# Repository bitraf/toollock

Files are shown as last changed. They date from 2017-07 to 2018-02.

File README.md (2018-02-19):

# TheLock
Electronic lock connected via wireless (Wi-Fi) and MQTT using [MsgFlo](https://msgflo.org).
The lock is intended to enforce 'checking out' and 'checking in' portable tools in a shared workshop environment.

It makes it possible to:

* Know whether a tool is currently in its station
* Checking for neccesary safety course before allowing usage
* Holding people responsible when equipment is not get returned or broken

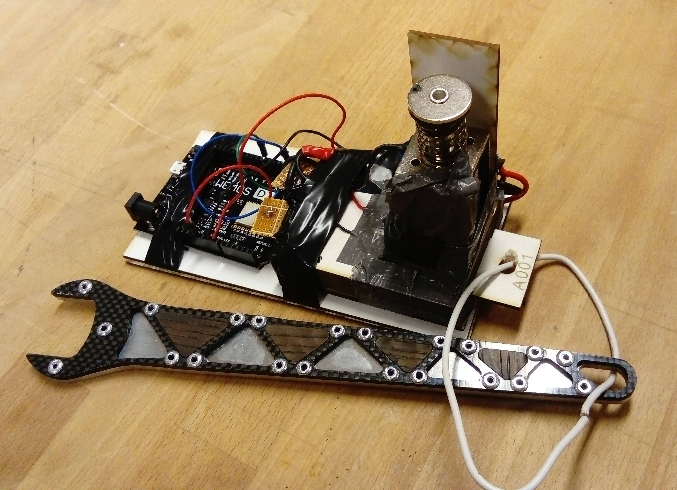
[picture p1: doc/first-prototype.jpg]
First funtional prototype


Each lock has a key with a matching key pattern. The key is physically attached to the tool using a wire.
An optical sensor detects that the right key is used. IR leds normally light through, only a matching key will fully block light.

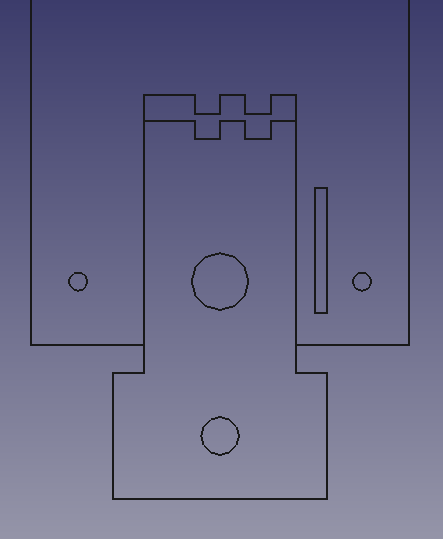
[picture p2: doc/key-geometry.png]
Key & lock geometry


The key and lock can be CNC-milled, lasercut or 3d-printed.

## Status
**Proof of concept**

* July 2017: Functional prototype was built during 2-day hackathon
* First production version planned for October 2017

## Bill of Materials

[Google Doc](https://docs.google.com/spreadsheets/d/1zNnj4h8AQoaYpxoNCeb7HHqZF6n6yWtV7tDY7eSM0z4/edit?usp=sharing)

* Microcontroller - ESP8266 or similar. We used a Wemos D1 board.
* actuator - we used a solenoid that is rated for 12V (it actually actuates at about 7V, but slowly), it draws about 0.3 - 0.7 A. Alternatives:
[1](https://www.banggood.com/12V-24V-Electronic-Door-Lock-Rfid-Access-Control-for-Cabinet-Drawer-p-1011146.html)
[2](https://www.banggood.com/12V-DC-Cabinet-Door-Drawer-Electric-Lock-Assembly-Solenoid-Lock-27x29x18mm-p-1048590.html)
* mosfet - we used a IPP055N03L
* resistor - a 10k ohm resistor for pulldown on the control signal
* power supply - a 12V DC power supply for the actuator / solenoid
* IR led 0805, 120deg. [Kingbright kp-2012f3c](http://no.farnell.com/kingbright/kp-2012f3c/led-ir-0805-940nm/dp/2290432)
* IR phototransistor 0805, 120 deg. [Kingbright kp-2012p3c](http://no.farnell.com/kingbright/kp-2012p3c/phototransistor-0805-940nm/dp/2290434)

https://wiki.wemos.cc/products:d1:d1_mini
https://github.com/esp8266/esp8266-wiki/wiki/Pin-definition

## Setup firmware

* Install Arduino libraries [PubsubClient](https://github.com/knolleary/pubsubclient) and [Msgflo](https://github.com/msgflo/msgflo-arduino)
* Setup wifi connection: Add a file `Config.h` defining parameters `WIFI_SSID` and `WIFI_PASSWORD`
* Configure MQTT details in the sketch

## TODO

v1.0: First fabricated version

* Electronics: Switch to a standard transmissive detector, PCB mounted.
* Mechanics: Update to vertical PCB orientation, check connections
* Produce initial 4 locks
* Mechanics: Add a casing/box for 4-8 locks. Securely wall/table mountable.

## License
MIT

## Made by

[einsmein](https://github.com/einsmein), [tingox](https://github.com/tingox) and [jonnor](https://github.com/jonnor)

## State machine

State machine diagram

## Electronics

Developed in KiCAD.
Schemantic used for first protototype

## Mechanics

Developed in FreeCAD.
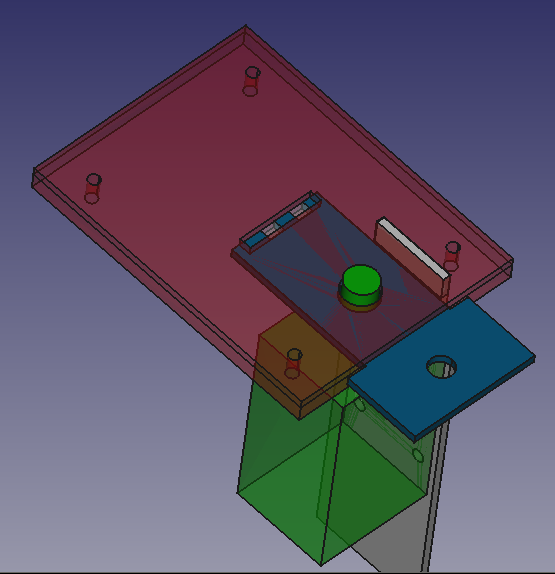
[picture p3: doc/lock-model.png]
Lock model


SIG: gnd+in
PWR: 12v+gnd
OUT: 12v+out

IN
GND
12v
12v
OUT

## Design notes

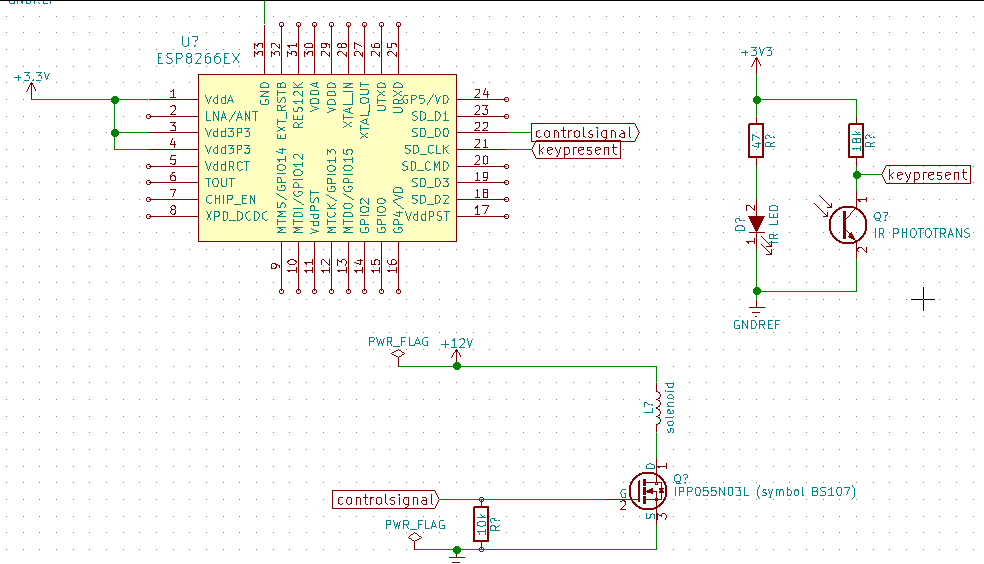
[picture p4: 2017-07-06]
doc/schematic.png

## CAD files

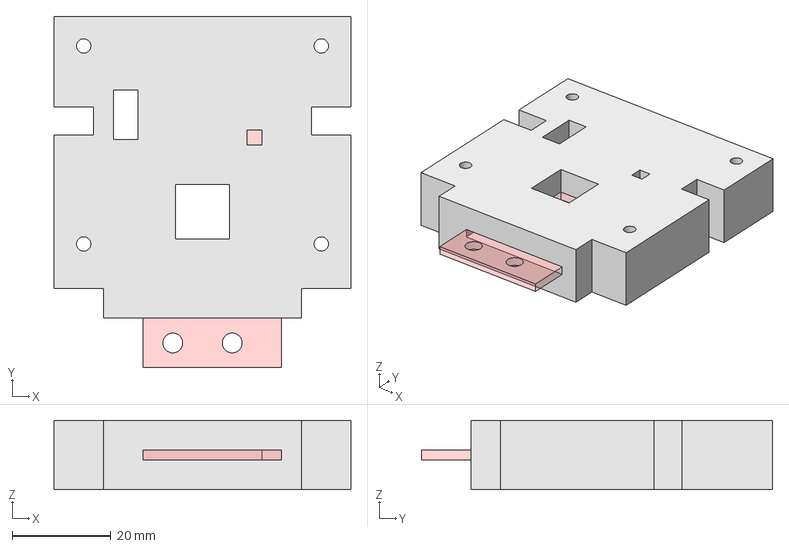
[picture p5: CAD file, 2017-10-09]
mechanics/toollock.fcstd
60.0 x 71.0 x 14.0 mm

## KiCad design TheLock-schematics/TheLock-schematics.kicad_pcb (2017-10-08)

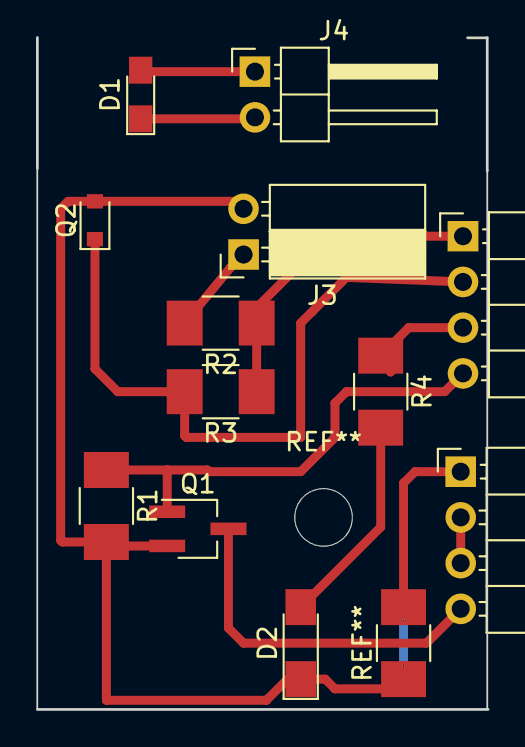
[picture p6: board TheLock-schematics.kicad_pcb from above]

Board: 2 copper layers, 25.0 x 37.3 mm, 12 parts (0 on the bottom side), 11 nets.

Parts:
D1: IR LED; LED_0805_HandSoldering
D2: LED; LED_1206_HandSoldering
J1: CONN_SIGNAL; Pin_Header_Angled_1x04_Pitch2.54mm
J2: CONN_POWER; Pin_Header_Angled_1x04_Pitch2.54mm
J3: CONN_IRBOARD; Socket_Strip_Angled_1x02_Pitch2.54mm
J4: CONN_IRLED; Pin_Header_Angled_1x02_Pitch2.54mm
Q1: PMV20XNE; SOT-23W_Handsoldering
Q2: IR PHOTOTRANS; D_0805
R1: 10k; R_1210_HandSoldering
R2: 47; R_1210_HandSoldering
R3: 18k; R_1210_HandSoldering
R4: R; R_1210_HandSoldering

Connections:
+3V3: J1.1, R2.1, R3.1
GNDPWR: D2.1, J2.1, J3.2, Q1.2, Q2.2, R1.2
unnamed: D1.1, J4.2
unnamed: D1.2, J4.1
unnamed: D2.2, R4.2
unnamed: J3.1, R2.2
keypresent: J1.2, Q2.1, R3.2
solenoid+: J2.2, J2.3
solenoid-: J2.4, Q1.3
status: J1.3, R4.1
unlock: J1.4, Q1.1, R1.1

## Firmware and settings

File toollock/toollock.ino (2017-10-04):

#include "./Config.h"
#include "./toollock.hpp"

#include <WiFiClient.h>
#include <WiFiClientSecure.h>
#include <ESP8266WiFi.h>

#include <PubSubClient.h>
#include <Msgflo.h>

#include "./participant.hpp"

// Configuration
ToolLockParticipant participants[] = {
  ToolLockParticipant("a001", D5, D0, D6),
  ToolLockParticipant("a002", D1, D2, D3),
  ToolLockParticipant("a003", D4, D7, D8),
};

static const char *MQTT_PREFIX = "public/toollock/";

// Defaults
#ifndef MQTT_PORT 
#define MQTT_PORT 1883
#endif
#ifndef MQTT_USERNAME
#define MQTT_USERNAME nullptr
#endif
#ifndef MQTT_PASSWORD
#define MQTT_PASSWORD nullptr
#endif

WiFiClient wifiClient;
PubSubClient mqttClient;
msgflo::Engine *engine;

void setup() {
  Serial.begin(115200);
  delay(100);
  Serial.println();

  const char *ssid = WIFI_SSID;
  Serial.printf("Configuring wifi: %s\r\n", ssid);
  WiFi.begin(ssid, WIFI_PASSWORD);

  mqttClient.setServer(MQTT_HOST, MQTT_PORT);
  mqttClient.setClient(wifiClient);

  String clientId = MQTT_PREFIX;
  clientId += WiFi.macAddress();

  engine = msgflo::pubsub::createPubSubClientEngine(mqttClient);
  engine->setClientId(clientId.c_str());
  engine->setCredentials(MQTT_USERNAME, MQTT_PASSWORD);
  engine->setTopicPrefix(MQTT_PREFIX);

  for (auto &p : participants) {
    engine->addParticipant(p);
    p.setup();
  }
}

void loop() {
  static bool connected = false;

  if (WiFi.status() == WL_CONNECTED) {
    if (!connected) {
      Serial.printf("Wifi connected: ip=%s\r\n", WiFi.localIP().toString().c_str());
    }
    connected = true;
    engine->loop();
  } else {
    if (connected) {
      connected = false;
      Serial.println("Lost wifi connection.");
    }
  }

  for (auto &p : participants) {
    p.loop();
  }
}

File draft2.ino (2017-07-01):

#include <WiFiClient.h>
#include <WiFiClientSecure.h>
#include <ESP8266WiFi.h>

#include <PubSubClient.h>
#include <Msgflo.h>

#include "./Config.h"

struct Config {
  const String role = "public/toollock/1";

  const int ledPin = D4;
  const int lockPin = D0;

  const String wifiSsid = WIFI_SSID;
  const String wifiPassword = WIFI_PASSWORD;

  const char *mqttHost = "mqtt.bitraf.no";
  const int mqttPort = 1883;

  const char *mqttUsername = "myuser";
  const char *mqttPassword = "mypassword";
} cfg;

WiFiClient wifiClient;
PubSubClient mqttClient;
msgflo::Engine *engine;
msgflo::InPort *lockPort;
long nextButtonCheck = 0;

const auto participant = msgflo::Participant("iot/TheLock", cfg.role);

void setup() {
  Serial.begin(115200);
  delay(100);
  Serial.println();
  Serial.println();
  Serial.println();

  Serial.printf("Configuring wifi: %s\r\n", cfg.wifiSsid.c_str());
  WiFi.begin(cfg.wifiSsid.c_str(), cfg.wifiPassword.c_str());

  mqttClient.setServer(cfg.mqttHost, cfg.mqttPort);
  mqttClient.setClient(wifiClient);

  String clientId = cfg.role;
  clientId += WiFi.macAddress();

  engine = msgflo::pubsub::createPubSubClientEngine(participant, &mqttClient, clientId.c_str());

//  lockPort = engine->addOutPort("button-event", "any", cfg.role + "/event");

  lockPort = engine->addInPort("lock", "boolean", cfg.role+"/lock",
  [](byte *data, int length) -> void {
      const std::string in((char *)data, length);
      const boolean on = (in == "1" || in == "true");
      Serial.printf("data: %s/n", in.c_str());
      digitalWrite(cfg.lockPin, on);
  });

  
  Serial.printf("Led pin: %d\r\n", cfg.ledPin);
  Serial.printf("Button pin: %d\r\n", cfg.lockPin);

  pinMode(cfg.lockPin, OUTPUT);
//  pinMode(cfg.ledPin, OUTPUT);
}

void loop() {
  static bool connected = false;

  if (WiFi.status() == WL_CONNECTED) {
    if (!connected) {
      Serial.printf("Wifi connected: ip=%s\r\n", WiFi.localIP().toString().c_str());
    }
    connected = true;
    engine->loop();
  } else {
    if (connected) {
      connected = false;
      Serial.println("Lost wifi connection.");
    }
  }

  // TODO: check for statechange. If changed, send right away. Else only send every 3 seconds or so
//  if (millis() > nextButtonCheck) {
//    const bool pressed = digitalRead(cfg.lockPin);
//    lockPort->send(pressed ? "true" : "false");
//    nextButtonCheck += 100;
//  }

//  digitalWrite(cfg.ledPin, !b);
}

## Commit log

2017-07-01 added initial schematics (in KiCad) for the circuit.
    [TheLock-schematics.kicad_pcb, TheLock-schematics.sch]
2017-07-02 Fixed the code for MC and added fake button code
    [draft2.ino]
2017-07-02 updated Kicad schematics
2017-07-02 Added light sensor
2017-07-04 schematics: Add optical key sensor
    [TheLock-schematics.sch]
2017-07-06 Add mechanical model
    [toollock.fcstd]
2017-09-16 README: Put a link to BOM google doc
2017-09-16 mechanics: Update to cabinet lock
    [toollock.fcstd]
2017-09-28 mechanics: Update to fit received solenoids
    Was a bit larger than specified, had to be moved 5mm in
    [toollock.fcstd]
2017-10-02 firmware: Avoid always sending state, only unlock in takeTool
    [toollock.ino]
2017-10-02 firmware: Validate input and report errors
    [toollock.ino]
2017-10-02 firmware: Fix wrong portname for error
    [toollock.ino]
2017-10-03 electronics: Update to the lock driver board
    Will have header connectors, so that 3-4 of them
    can be connected to a single ESP8266 module
    [TheLock-schematics.sch]
2017-10-03 electronics: Rough layout of lock board
    [TheLock-schematics.sch]
2017-10-04 firmware: Add status LED, 3x locks per micro
2017-10-05 electronics: PCB layout and mechanics should conform now
    IR phototrans and LED should be positioned OK
    PCB size and attachment should be roughly OK
    [TheLock-schematics.kicad_pcb, TheLock-schematics.sch, toollock.fcstd]
2017-10-08 electronics: Update to better accommodate LED
    [TheLock-schematics.kicad_pcb, toollock.fcstd]
2017-10-08 mechanics: Forgot update
    [toollock.fcstd]
2017-10-09 mechanics: Also add text to generated keys
    [toollock.fcstd]
2017-10-09 mechanics: Group generated keygeometry
    [toollock.fcstd]
